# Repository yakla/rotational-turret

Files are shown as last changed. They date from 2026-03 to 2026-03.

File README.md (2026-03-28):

# infinit Rotational Smart Tracking Camera

first i started the project as a idea for a consept for a rotating turret that can go forever without needing to retract. i wanted to make it a concept so i made the build realy small but after i designed the base and then decited to go all out and make a follower cammera. in the end it ended up super small in just 10cm×10cm×9cm. for me its just a fun project to do in the meantime of the war currently. 

## Mechanics & Power
The project uses a high speed brushless motor to rotate the base gear and a very small servo to rotate the head.
The power uses usb c 12v and buck convertor to power everything and passes the data and the power throught a slip ring  inside the shaft .

## Communication & Vision Pipeline
To comunicate with other devices and transfer the stream it uses a udp server to get the ip of the device and send back the camera data to it for high speed transfer and low cpu usage on the small esp . 
It also uses bluetooth for manual movment mode. 
For the color pipeline i use a optimised version of rgb to hsv and color range checking for each pixel summing the position and getting the aproximet position to rotate to.

## Modes
the turret has 3 main modes.
* Manual that streams with jpeg optimised stream and let the user control the turret
* Follower that sets the turret to follow the target (for now set in the code)
* Lock that send the data of the target position without following it

## Design & Hardware
For the head i designed a costume pcb to fit the tof sensor the esp camera and the leds.
For a encloseure i use a thin sheet of invisable plastic that rotates with the turret. that make it realy cool in my opinion.

CAD Link : https://cad.onshape.com/documents/5493d3bfb7c584824d124c44/w/b9fe300d7cd71857bff2772f/e/d3c804d532ca15a2a7af37b9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

For the Hardware i used:
* XIAO ESP32-S3 - Main Controller & Vision Processing
* PTK 7308H Servo - Pan/Tilt Movement
* Emax ECO 1407 Motor - Turret Movement
* Custom PCB - Power distribution, Leds & sensor integration
*  - Distance detection (ToF)
   - Camera OV2640
   - SK6805 NeoPixel

Screenshot 2026-03-17 at 10-38-05 inf turret turret assembly





## Project Status & Roadmap
- [ ] Mobile App for Remote control and setting Wifi detection and simple viewing window (Planned)
- [x] Design the project with a cheaper servo (Planned) 

## How to use
* **Build:** Use PlatformIO to flash the Firmware/ folder to the XIAO.
* **Setup_bluetooth:** Connect to the device via Bluetooth.
* **Setup_wifi:** Currently have to set it in the main code. will probebly add a way in the app later
* **UDP_client** you can use the python code in tools folder of the firmware currently. Will add a viewing window in the app later
* **Run:** Point the camera at a target object; the turret will lock on using the HSV threshold defined in config.h.

## Credits
* Designed and built as part of Hack Club.

## BOM
| Item | Description | Quantity | Unit Price ($) | Total Price ($) | URL |
|:---|:---|:---|:---|:---|:----|
| Hobbywing Skywalker 12A | esc for the brushless motor | 1 | $5.23 | $5.23 | https://he.aliexpress.com/item/1005006848267224.html |
| Emax ECO 1407 Motor 2800KV | the brushless motor for the base turret rotation | 1 | $12.39 | $16.11 | https://he.aliexpress.com/item/1005006857011061.html |
| Ptk 7308h | the servo that moves the head of the camera | 1 | $27.00 | $27.16 | https://he.aliexpress.com/item/1005005891940798.html |
| slip ring 6.5mm 8ch a1 | the most important part to move electucity even when rotating | 1 | $4.04 | $7.04 | https://he.aliexpress.com/item/1005009463382321.html |
| USB-C PD PD/QC Decoy Board | the usb port | 1 | $1.30 | $1.30 | https://he.aliexpress.com/item/1005005622939899.html |
| Mini360 buck convertor | get the usb voltage down | 1 | $0.28 | $1.74 |https://he.aliexpress.com/item/1005008724925620.html |
| XIAO ESP32-S3 Sense | the brain | 1 | $13.85 | $17.21 | https://he.aliexpress.com/item/1005005544155799.html |
| Adafruit VL53L4CX | the tof sensor | 1 | $19.57 | $19.57 | https://he.aliexpress.com/item/1005010327402661.html |
| SK6805 2427 | neopixel for the pcb | 1 (50 in one order)  | $3.73 | $6.30 | https://he.aliexpress.com/item/1005008979678361.html|
| capcacitor 100nf 0805 | just there for the neopixel | 1 (100 in one order) | $1.24 | $1.24 | https://he.aliexpress.com/item/1005005293453925.html |
| capcacitor 10uf 1206 | just there for the neopixel | 1 (20 in one order)  | $1.35 | $1.35 | https://he.aliexpress.com/item/1005007363840397.html |
| resestor 47R 0805 | for the neopixel din | 1 (100 in one order) | $1.11 | $1.11 | https://he.aliexpress.com/item/32382494431.html |
|o-ring thickring 2mm 26mm od |for the conveyor of the head spin |1(100 in one order) |1.99$ |$1.99 |https://he.aliexpress.com/item/1005006851111300.html |
|PCB 	 |the PCB	 |1 (5 for one order)	 |$2.00	 |$7.29|https://www.elecrow.com
|6000-2RS Bearing 10mm id 26mm od|for low friction shaft rotation|1 (4 for one order)|$3.12|$3.12|https://he.aliexpress.com/item/1005006079201259.html|
|Clamp shaft lock Ring Collar 10mm|to hold the shaft better|1|$2.73|$2.73|https://he.aliexpress.com/item/1005006211797860.html|
**Sum** |                                                               |                      | **$100.93** | **$120.49** current price **$105.10** | |

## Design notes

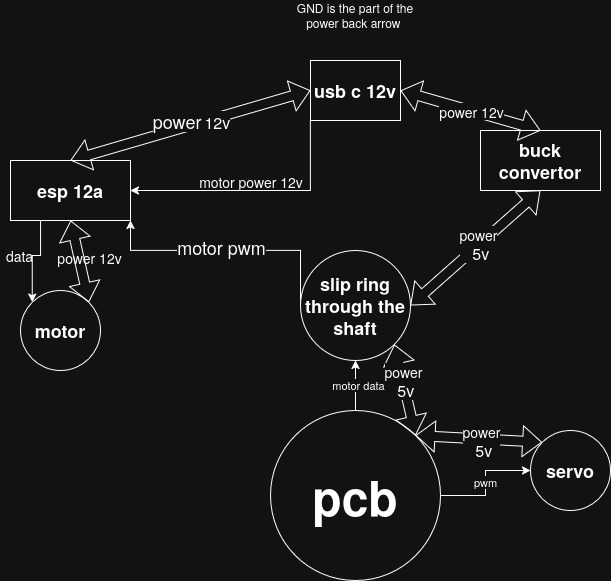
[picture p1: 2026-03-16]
Turret diagram.jpg

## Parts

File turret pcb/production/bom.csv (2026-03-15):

Designator | Footprint | Quantity | Value | LCSC Part #
_6, _5, _4, _3, _2, |  | 6
C1 | 0805 | 1 | 0.1µF
C2 | 1206 | 1 | 10µF
D2_12, D2_11, D2_10, D2_9, D2_8, D2_7, D2_6, D2_5, D2_4, D2_3, D2_2, D2 | LED_SK6805_PLCC4_2.4x2.7mm_P1.3mm | 12 | SK6805
J1 | PinHeader_1x06_P2.54mm_Vertical | 1 | Conn_01x06_Pin
J2 | PinHeader_1x04_P2.54mm_Vertical | 1 | Conn_01x04_Pin
R5 | 0805 | 1 | 470
U1 | xiao-esp32s3 | 1 | XIAO-ESP32S3

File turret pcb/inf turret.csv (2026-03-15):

Id | Designator | Footprint | Quantity | Designation | Supplier and ref
1 | D2,D2,D2,D2,D2,D2,D2,D2,D2,D2,D2,D2 | LED_SK6805_PLCC4_2.4x2.7mm_P1.3mm | 12 | SK6805
2 | J2 | PinHeader_1x04_P2.54mm_Vertical | 1 | Conn_01x04_Pin
3 | ,,,,, |  | 6
4 | R5 | R_0805_2012Metric | 1 | 470
5 | C2 | C_1206_3216Metric | 1 | 10µF
6 | J1 | PinHeader_1x06_P2.54mm_Vertical | 1 | Conn_01x06_Pin
7 | U1 | xiao-esp32s3 | 1 | XIAO-ESP32S3
8 | C1 | C_0805_2012Metric | 1 | 0.1µF

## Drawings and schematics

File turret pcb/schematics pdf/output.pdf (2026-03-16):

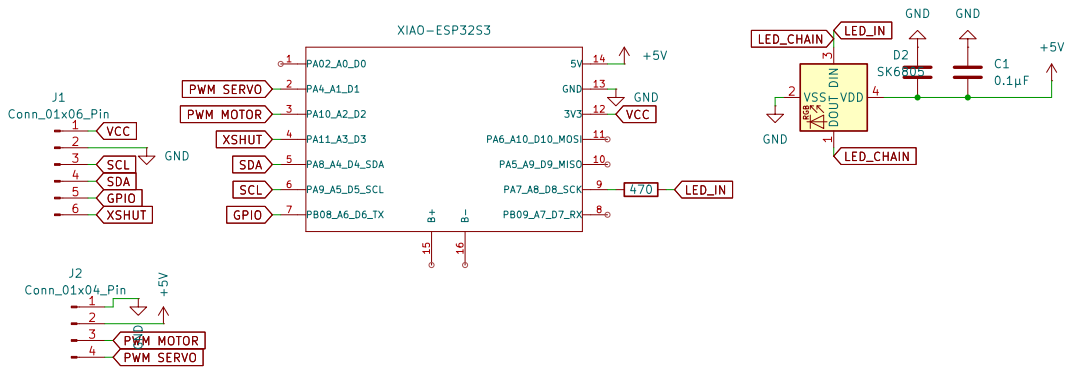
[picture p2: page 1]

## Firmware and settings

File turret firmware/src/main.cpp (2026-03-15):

#include <Arduino.h>
#include <ESP32Servo.h>
#include <esp_camera.h>
#include <FastLED.h>
#include <WiFi.h>
#include <Wire.h>

#include "secret.h"
#include "shared/app_state.h"
#include "ble/ble_control.h"
#include "camera/camera_stream.h"
#include "led/led_control.h"

#define CAMERA_UDP_PORT 12345


void colorPipeLineDetection();

void setup() {
    Serial.begin(115200);

    WiFi.begin(WIFI_SSID, WIFI_PASS);
    while (WiFiClass::status() != WL_CONNECTED) {
        delay(500);
        Serial.print(".");
    }
    Serial.println("\nWiFi connected");
    Serial.println(WiFi.localIP());

    CFastLED::addLeds<NEOPIXEL, constants::LED_DATA>(leds, constants::ledAmount);
    FastLED.setBrightness(70);
    Wire.begin(constants::TOF_SDA, constants::TOF_SCL);
    tof_sensor = VL53L4CX(&Wire, constants::TOF_XSHUT);

    turretMotor.attach(constants::MOTOR, 1000, 2000);
    headServo.attach(constants::SERVO, 0, 2048);

    setupBleControl();
    xTaskCreatePinnedToCore(
        LedControl,
        "LED_CONTROL",
        2048,
        nullptr,
        1,
        nullptr,
        0
    );

    if (setupCamera()) {
        cameraUdp.begin(CAMERA_UDP_PORT);
        xTaskCreatePinnedToCore(
            udp_stream_task, "udp_stream",
            8192,
            nullptr
            , 1,
            nullptr
            , 1);
    } else {
        Serial.println("Camera setup failed");
    }
}


void loop() {
    if (!remoteIp) ip_listener();
}

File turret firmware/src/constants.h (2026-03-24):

#ifndef INF_TURRET_CONSTANTS_H
#define INF_TURRET_CONSTANTS_H
#include "FastLED.h"
#include "detection/hsv_utils.h"

namespace constants {
    extern HsvPixel dog_min_hsv;
    extern HsvPixel dog_max_hsv; // example values are defined in constants.cpp

    enum Pins {
        MOTOR = 3,
        SERVO = 2,
        LED = 9,
        TOF_SCL = 6,
        TOF_SDA = 5,
        TOF_GPIO = 7,
        TOF_XSHUT = 4,
        LED_DATA = 9
    };
    constexpr int ledAmount = 12;
    constexpr uint8_t verticalFov = 43;
    constexpr uint8_t horizontalFov = 56;

    extern const CRGBPalette16 purplePalette;
    extern const CHSVPalette16 bluePalette;
}

#endif //INF_TURRET_CONSTANTS_H

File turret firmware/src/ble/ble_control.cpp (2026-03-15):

#include "ble_control.h"

#include <Arduino.h>
#include <NimBLEDevice.h>

#include "shared/app_state.h"

#define SERVICE_UUID "4cad297a1b0143df836d80c718cf3cd1"
#define DEVICE_NAME "TurretControl"

class RotationCallbacks : public NimBLECharacteristicCallbacks {
    void onWrite(NimBLECharacteristic* pCharacteristic, NimBLEConnInfo& connInfo) override {
        const std::string value = pCharacteristic->getValue();
        if (value.length() < 3) return;

        switch (value[2]) {
            case MANUAL_CONTROL:
                currentMode = MANUAL_CONTROL;
                turretMotor.writeMicroseconds(map(value[0], 0, 127, 1000, 2000));
                headServo.writeMicroseconds(map(value[1], 0, 127, 0, 2000));
                break;
            case FOLLOWER:
                currentMode = FOLLOWER;
                break;
            default:
                currentMode = LOCK;
                turretMotor.writeMicroseconds(1500);
                headServo.writeMicroseconds(1000);
                break;
        }
    }

    void onSubscribe(NimBLECharacteristic *pCharacteristic, NimBLEConnInfo &connInfo, uint16_t subValue) override {
        Serial.println("subscribe");
    }
};

void setupBleControl() {
    NimBLEDevice::init(DEVICE_NAME);
    pServer = NimBLEDevice::createServer();

    NimBLEService *pService = pServer->createService(SERVICE_UUID);
    NimBLECharacteristic *pRotationCharacteristic = pService->createCharacteristic("1234");
    pRotationCharacteristic->setCallbacks(new RotationCallbacks);

    pService->start();

    NimBLEAdvertising *pAdvertising = NimBLEDevice::getAdvertising();
    pAdvertising->addServiceUUID(SERVICE_UUID);
    pAdvertising->setName(DEVICE_NAME);
    pAdvertising->start();
}

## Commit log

2026-03-15 Initial clean commit
    [bom.csv, designators.csv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]
2026-03-15 add the constants Hsv filter
2026-03-15 Add footprints and schematics to the project folder
    [inf turret-B_Mask.gbr, inf turret-B_Paste.gbr, inf turret-B_Silkscreen.gbr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]
2026-03-15 Update CAD link in README.md
2026-03-15 Clean up README.md and remove duplicate CAD link
    Removed duplicate CAD link section and fixed minor typos.
2026-03-16 more updates
    [inf turret.kicad_pcb]
